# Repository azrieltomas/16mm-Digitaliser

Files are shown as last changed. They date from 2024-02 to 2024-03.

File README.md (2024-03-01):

# 16mm Digitaliser
A slight improvement on the [8mm Digitaliser](https://github.com/azrieltomas/8mm-Digitaliser)
This is currently a work in progress and not fully implemented.

### Design
The hardware design to capture the frames utilises a constantly running motor, and dual IR sensors to determine when sprocket perforations have passed.
As 5+ frames can fit on the digital capture, photographs are taken every 5 frames. Cropping will be acheived by automatically offsetting the crop zone and exporting to separate images.

### Parts
Parts for aligning the film and holding the sensors are from various 3D prints.

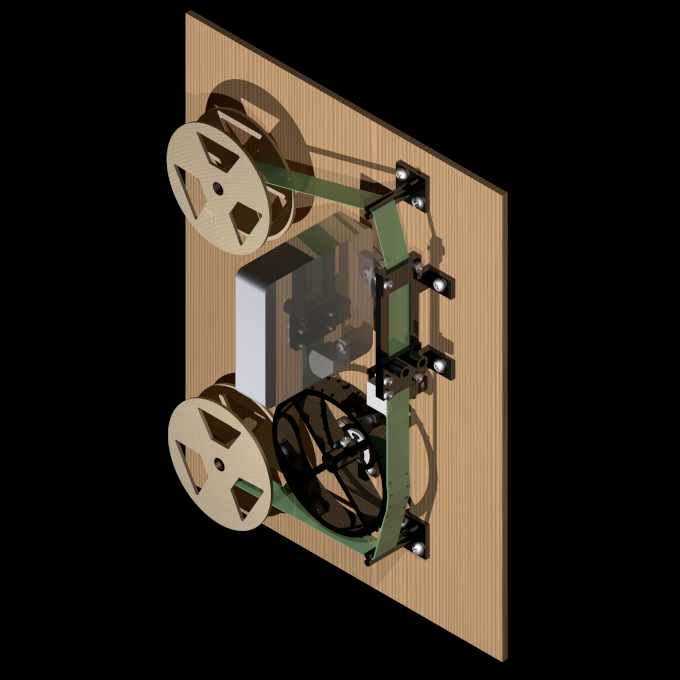
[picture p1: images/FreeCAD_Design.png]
Parts Design
\
*Physical Parts Layout (FreeCAD)*

### Controller
Each perforation sensor has two fine tuning methods:
* Gain (affects sensor output level)
* Cutoff (affects reference level).
The gain and cutoff signals are compared with an LM741 to determine if a perforation is sensed.This is adjustable to compensate for light sections along the film edge that are not perforations, but are still picked up by the sensor.Both perforation sensors are connected by an AND gate to a counter to further filter out non-perforations on single sides of the film.

For single perforation film, a switch sets the sense2 output to always on.

Once the counter has reaches four, it triggers the camera, and resets on five via an AND gate on QA and QC.

The motor can be switched on/off via a buffer circuit. I have used a BUL128 only because I have spares, and they're the only transistor on hand that can handle the motor current. It is probably wise to put a flyback diode on the motor.

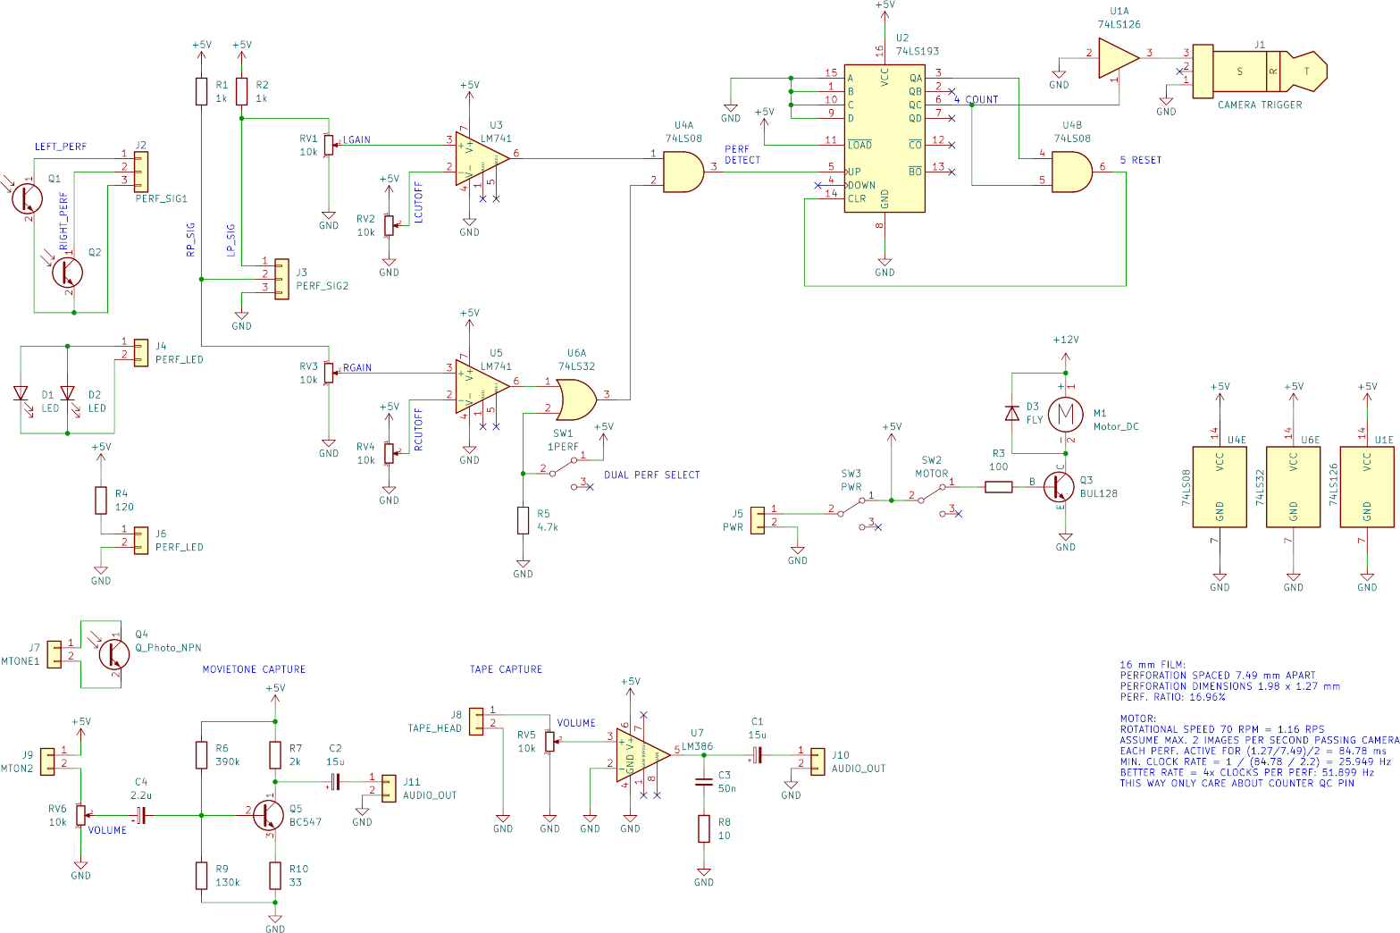
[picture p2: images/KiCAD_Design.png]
Circuit Design
\
*Controller Design (KiCAD)*

### Audio
Audio is captured in two ways, depending on the storage method.
Digital processing can be done by any additional system.

#### Standard magnetic audio
Audio is picked up by a modified cassette tape head and amplified by an LM386 for simplicity.

#### Movietone
Audio is converted by an IR phototransistor - theoretically the same one used for the second set of perforations in dual perf film.
A BC547 amplifier boosts this to line levels.

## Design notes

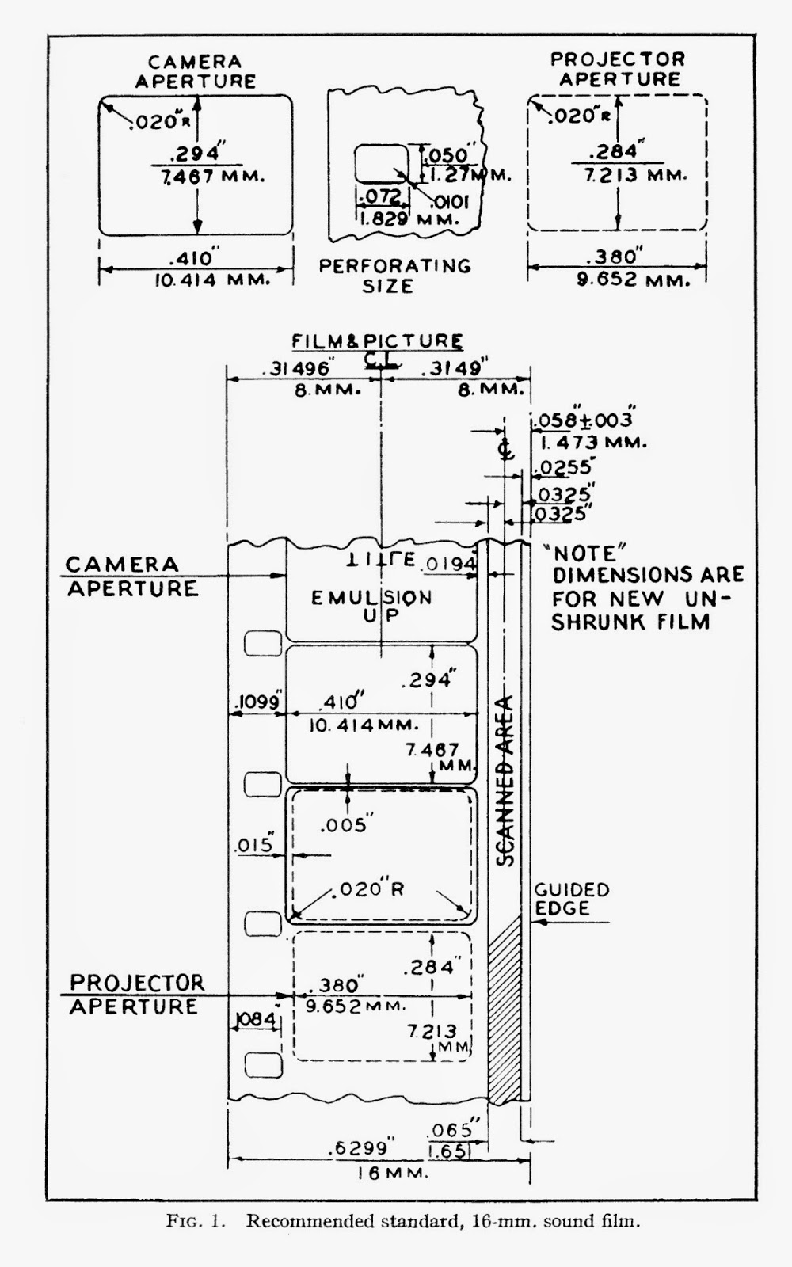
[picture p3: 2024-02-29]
Additional Tools/16mm Sound 1.jpg

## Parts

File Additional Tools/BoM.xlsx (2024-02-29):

Reference | Value | Datasheet | Footprint | Qty | DNP
C1,C2 | 15u | ~ | Capacitor_THT:C_Radial_D6.3mm_H5.0mm_P2.50mm | 2
C3 | 50n | ~ | Capacitor_THT:C_Rect_L4.6mm_W2.0mm_P2.50mm_MKS02_FKP02 | 1
C4 | 2.2u | ~ | Capacitor_THT:C_Radial_D6.3mm_H5.0mm_P2.50mm | 1
D1,D2 | LED | ~ | LED_THT:LED_D5.0mm | 2
D3 | FLY | ~ |  | 1
J1 | CAMERA TRIGGER | ~ | 2.5mm TRS Jack | 1
J2,J3 | Connector_JST:JST_EH_B3B-EH-A_1x03_P2.50mm_Vertical | ~ |  | 1
 |  |  |  | 1
J4,J6 | Connector_JST:JST_EH_B2B-EH-A_1x02_P2.50mm_Vertical | ~ |  | 2
J5,SW3 | PWR | ~ | -- mixed values -- | 2
J7 | MTONE1 | ~ | Connector_JST:JST_EH_B2B-EH-A_1x02_P2.50mm_Vertical | 1
J8 | TAPE_HEAD | ~ | Connector_JST:JST_EH_B2B-EH-A_1x02_P2.50mm_Vertical | 1
J9 | MTON2 | ~ | Connector_JST:JST_EH_B2B-EH-A_1x02_P2.50mm_Vertical | 1
J10,J11 | AUDIO_OUT | ~ | Connector_JST:JST_EH_B2B-EH-A_1x02_P2.50mm_Vertical | 2
J14 | POS1 | ~ | Connector_PinHeader_2.54mm:PinHeader_1x25_P2.54mm_Vertical | 1
J15 | POS2 | ~ | Connector_PinHeader_2.54mm:PinHeader_1x25_P2.54mm_Vertical | 1
J16 | NEG1 | ~ | Connector_PinHeader_2.54mm:PinHeader_1x25_P2.54mm_Vertical | 1
J17 | NEG2 | ~ | Connector_PinHeader_2.54mm:PinHeader_1x25_P2.54mm_Vertical | 1
M1 | Motor_DC | ~ | Connector_JST:JST_EH_B2B-EH-A_1x02_P2.50mm_Vertical | 1
Q1,Q2,Q4 | Q_Photo_NPN | ~ | LED_THT:LED_D5.0mm | 3
Q3 | BUL128 | ~ | Package_TO_SOT_THT:TO-220-3_Vertical | 1
Q5 | BC547 | https://www.onsemi.com/pub/Collateral/BC550-D.pdf | Package_TO_SOT_THT:TO-92_Inline | 1
R1,R2 | 1k | ~ | Resistor_THT:R_Axial_DIN0207_L6.3mm_D2.5mm_P7.62mm_Horizontal | 2
R3 | 100 | ~ | Resistor_THT:R_Axial_DIN0207_L6.3mm_D2.5mm_P7.62mm_Horizontal | 1
R4 | 120 | ~ | Resistor_THT:R_Axial_DIN0207_L6.3mm_D2.5mm_P7.62mm_Horizontal | 1
R5 | 4.7k | ~ | Resistor_THT:R_Axial_DIN0207_L6.3mm_D2.5mm_P7.62mm_Horizontal | 1
R6 | 390k | ~ | Resistor_THT:R_Axial_DIN0207_L6.3mm_D2.5mm_P7.62mm_Horizontal | 1
R7 | 2k | ~ | Resistor_THT:R_Axial_DIN0207_L6.3mm_D2.5mm_P7.62mm_Horizontal | 1
R8 | 10 | ~ | Resistor_THT:R_Axial_DIN0207_L6.3mm_D2.5mm_P7.62mm_Horizontal | 1
R9 | 130k | ~ | Resistor_THT:R_Axial_DIN0207_L6.3mm_D2.5mm_P7.62mm_Horizontal | 1
R10 | 33 | ~ | Resistor_THT:R_Axial_DIN0207_L6.3mm_D2.5mm_P7.62mm_Horizontal | 1
RV1,RV2,RV3,RV4,RV5,RV6 | 10k | ~ | -- mixed values -- | 6
SW1 | 1PERF | ~ | Connector_PinSocket_2.54mm:PinSocket_1x03_P2.54mm_Vertical | 1
SW2 | MOTOR | ~ | Connector_PinSocket_2.54mm:PinSocket_1x03_P2.54mm_Vertical | 1
U1 | 74LS126 | http://www.ti.com/lit/gpn/sn74LS126 | Package_DIP:DIP-14_W7.62mm_Socket | 1
U2 | 74LS193 | http://www.ti.com/lit/ds/symlink/sn74ls193.pdf | Package_DIP:DIP-16_W7.62mm_Socket | 1
U3,U5 | LM741 | http://www.ti.com/lit/ds/symlink/lm741.pdf | Package_DIP:DIP-8_W7.62mm_Socket | 2
U4 | 74LS08 | http://www.ti.com/lit/gpn/sn74LS08 | Package_DIP:DIP-14_W7.62mm_Socket | 1
U6 | 74LS32 | http://www.ti.com/lit/gpn/sn74LS32 | Package_DIP:DIP-14_W7.62mm_Socket | 1
U7 | LM386 | http://www.ti.com/lit/ds/symlink/lm386.pdf | Package_DIP:DIP-8_W7.62mm_Socket | 1

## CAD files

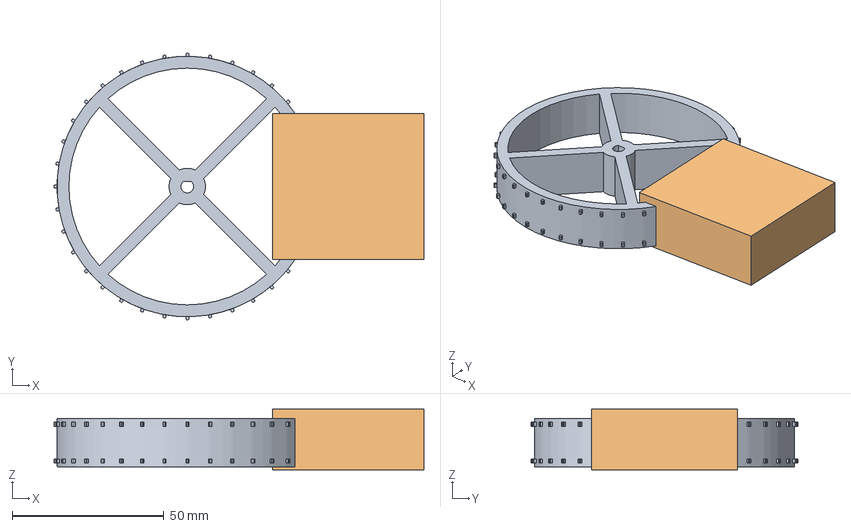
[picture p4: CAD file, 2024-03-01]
3D_Prints/16mm Sprocket.FCStd
121.9 x 87.8 x 20.0 mm

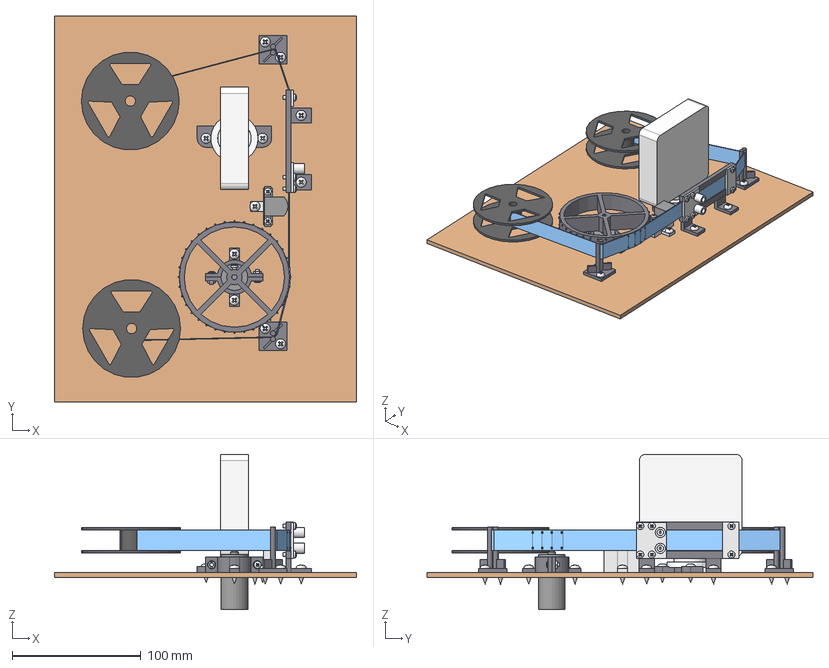
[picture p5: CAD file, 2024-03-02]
3D_Prints/Layout/Layout.FCStd
235.0 x 300.0 x 121.0 mm
Motor
Bracket1
Bracket2
DrivingWheel
MainHolder002
Reel
Horseshoe
Lamp
TapeHead
Reel001
Guide
Guide001
Base
Film
TapeHeadBase
4 mmx12-Screw
4 mmx12-Screw001
4 mmx12-Screw002
4 mmx12-Screw003
4 mmx12-Screw004
4 mmx12-Screw005
4 mmx12-Screw006
4 mmx12-Screw007
4 mmx12-Screw008
4 mmx12-Screw009
4 mmx12-Screw010
M3x8-Screw
M3-Nut
M3-Nut001
M3x8-Screw001
4 mmx12-Screw011
4 mmx12-Screw012
M3x8-Screw013
M3x8-Screw003
M3x8-Screw005
M3x8-Screw007
M3x8-Screw008
M3x8-Screw009
M3x8-Screw010
M3x8-Screw011
M3x8-Screw012
TopCover001
BottomCover001

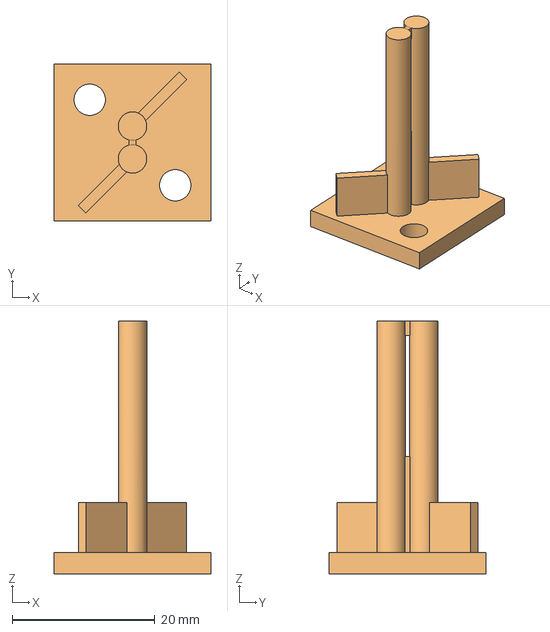
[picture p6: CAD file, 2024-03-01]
3D_Prints/16mm Film Guide.FCStd
22.0 x 22.0 x 35.5 mm

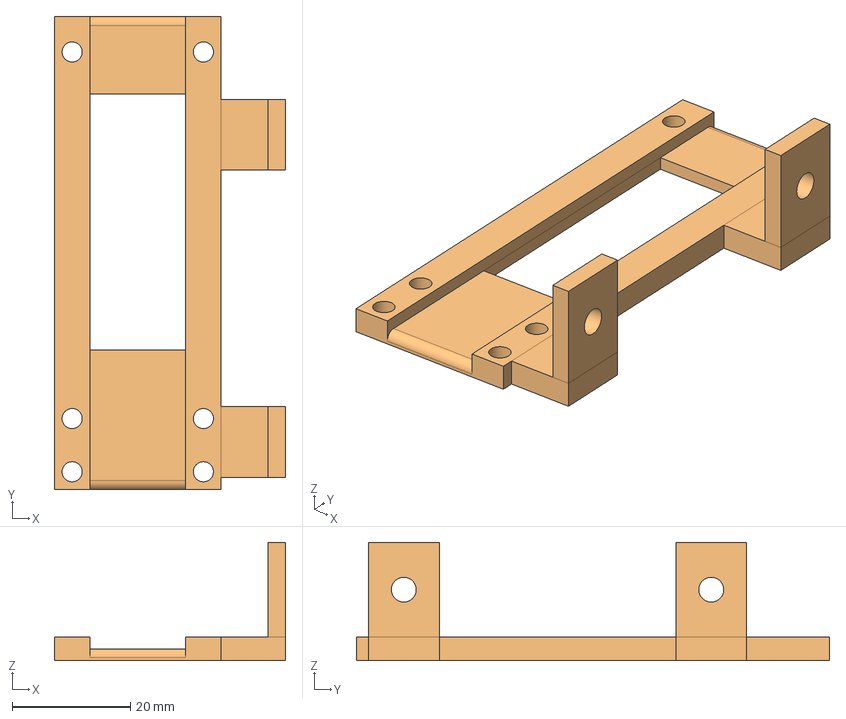
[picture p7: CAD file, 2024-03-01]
3D_Prints/16mm Film Holder.FCStd
39.1 x 80.0 x 20.0 mm
MainHolder
MainHolder001

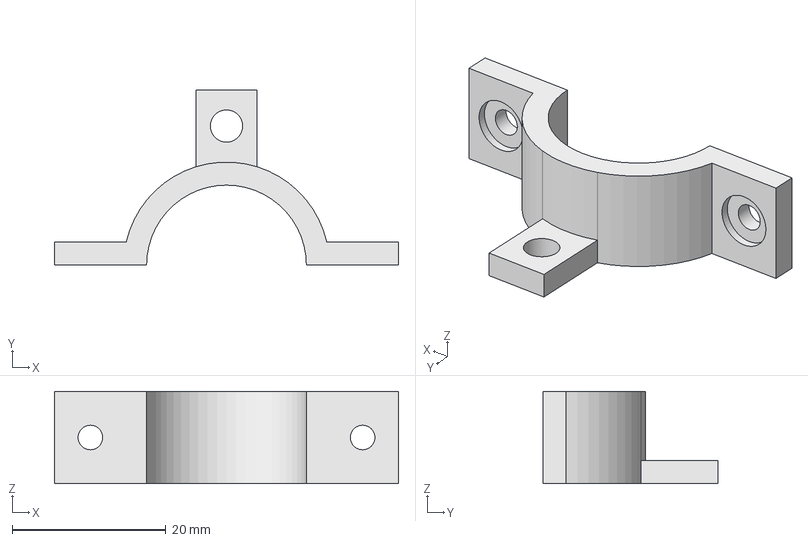
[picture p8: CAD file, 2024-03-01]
3D_Prints/Motor Bracket.FCStd
44.8 x 22.8 x 12.0 mm

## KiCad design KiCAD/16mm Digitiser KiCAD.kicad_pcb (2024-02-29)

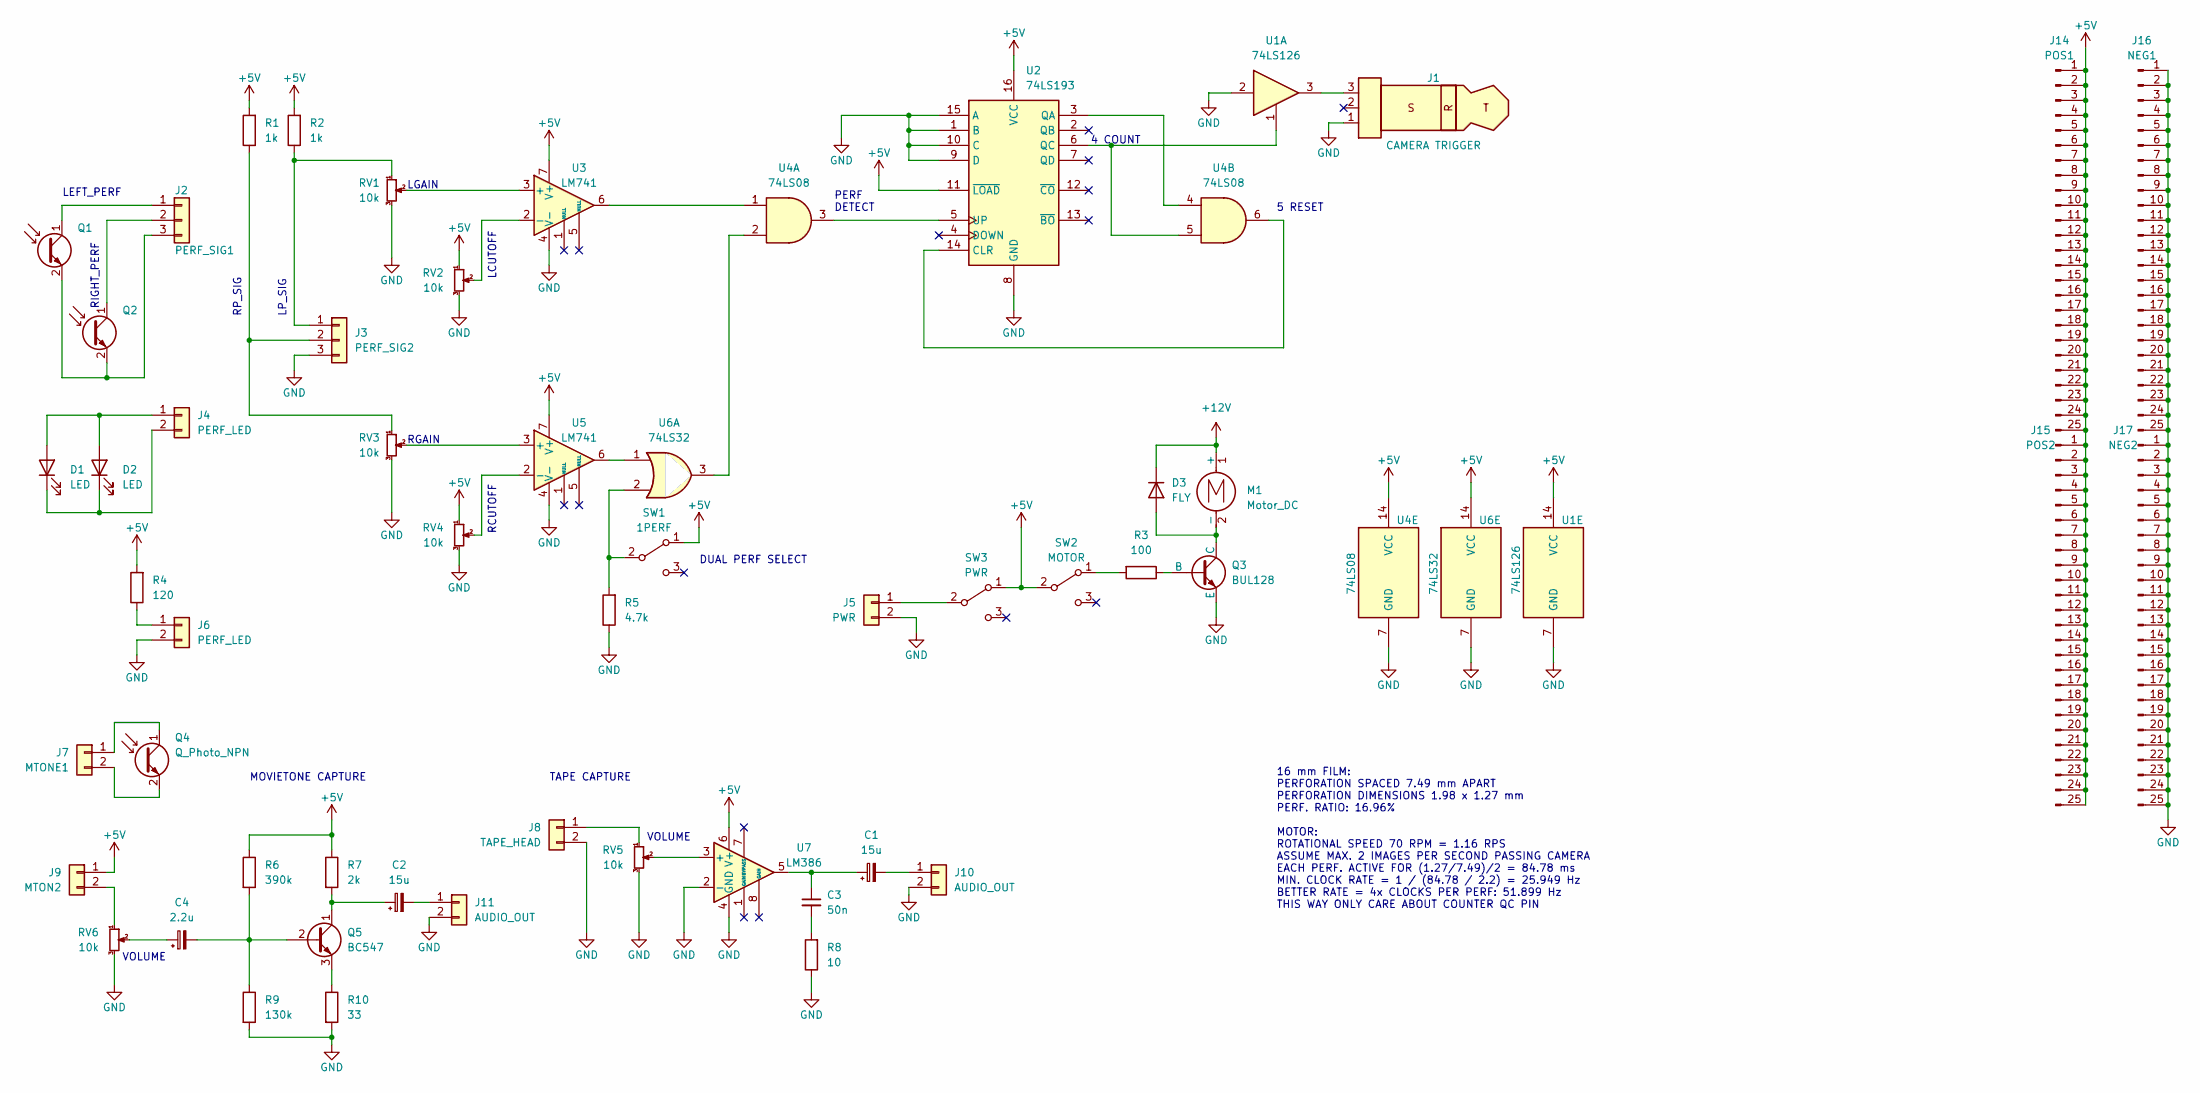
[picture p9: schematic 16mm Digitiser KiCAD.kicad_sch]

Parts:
C1, C2: 15u; C_Radial_D6.3mm_H5.0mm_P2.50mm
C3: 50n; C_Rect_L4.6mm_W2.0mm_P2.50mm_MKS02_FKP02
C4: 2.2u; C_Radial_D6.3mm_H5.0mm_P2.50mm
D1, D2: LED; LED_D5.0mm
D3: FLY
J1: CAMERA TRIGGER; JST_EH_B3B-EH-A_1x03_P2.50mm_Vertical
J2: PERF_SIG1; JST_EH_B3B-EH-A_1x03_P2.50mm_Vertical
J3: PERF_SIG2; JST_EH_B3B-EH-A_1x03_P2.50mm_Vertical
J4, J6: PERF_LED; JST_EH_B2B-EH-A_1x02_P2.50mm_Vertical
J5: PWR; JST_EH_B2B-EH-A_1x02_P2.50mm_Vertical
J7: MTONE1; JST_EH_B2B-EH-A_1x02_P2.50mm_Vertical
J8: TAPE_HEAD; JST_EH_B2B-EH-A_1x02_P2.50mm_Vertical
J9: MTON2; JST_EH_B2B-EH-A_1x02_P2.50mm_Vertical
J10, J11: AUDIO_OUT; JST_EH_B2B-EH-A_1x02_P2.50mm_Vertical
J14: POS1; PinHeader_1x25_P2.54mm_Vertical
J15: POS2; PinHeader_1x25_P2.54mm_Vertical
J16: NEG1; PinHeader_1x25_P2.54mm_Vertical
J17: NEG2; PinHeader_1x25_P2.54mm_Vertical
M1: Motor_DC; JST_EH_B2B-EH-A_1x02_P2.50mm_Vertical
Q1, Q2, Q4: Q_Photo_NPN; LED_D5.0mm
Q3: BUL128; TO-220-3_Vertical
Q5: BC547; TO-92_Inline
R1, R2: 1k; R_Axial_DIN0207_L6.3mm_D2.5mm_P7.62mm_Horizontal
R3: 100; R_Axial_DIN0207_L6.3mm_D2.5mm_P7.62mm_Horizontal
R4: 120; R_Axial_DIN0207_L6.3mm_D2.5mm_P7.62mm_Horizontal
R5: 4.7k; R_Axial_DIN0207_L6.3mm_D2.5mm_P7.62mm_Horizontal
R6: 390k; R_Axial_DIN0207_L6.3mm_D2.5mm_P7.62mm_Horizontal
R7: 2k; R_Axial_DIN0207_L6.3mm_D2.5mm_P7.62mm_Horizontal
R8: 10; R_Axial_DIN0207_L6.3mm_D2.5mm_P7.62mm_Horizontal
R9: 130k; R_Axial_DIN0207_L6.3mm_D2.5mm_P7.62mm_Horizontal
R10: 33; R_Axial_DIN0207_L6.3mm_D2.5mm_P7.62mm_Horizontal
RV1, RV2, RV3, RV4: 10k; Potentiometer_ACP_CA9-V10_Vertical
RV5, RV6: 10k; Potentiometer_Alps_RK163_Single_Horizontal
SW1: 1PERF; PinSocket_1x03_P2.54mm_Vertical
SW2: MOTOR; PinSocket_1x03_P2.54mm_Vertical
SW3: PWR; PinSocket_1x03_P2.54mm_Vertical
U1: 74LS126; DIP-14_W7.62mm_Socket
U2: 74LS193; DIP-16_W7.62mm_Socket
U3, U5: LM741; DIP-8_W7.62mm_Socket
U4: 74LS08; DIP-14_W7.62mm_Socket
U6: 74LS32; DIP-14_W7.62mm_Socket
U7: LM386; DIP-8_W7.62mm_Socket

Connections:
+5V: J9.1, J14.1, J14.2, J14.3, J14.4, J14.5, J14.6, J14.7, J14.8, J14.9, J14.10, J14.11, J14.12, J14.13, J14.14, J14.15, J14.16, J14.17, J14.18, J14.19, J14.20, J14.21, J14.22, J14.23, J14.24, J14.25, J15.1, J15.2, J15.3, J15.4, J15.5, J15.6, J15.7, J15.8, J15.9, J15.10, J15.11, J15.12, J15.13, J15.14, J15.15, J15.16, J15.17, J15.18, J15.19, J15.20, J15.21, J15.22, J15.23, J15.24, J15.25, R1.2, R2.2, R4.2, R6.1, R7.1, RV2.1, RV4.1, SW1.1 (A), SW2.2 (B), SW3.1 (A), U1.14 (VCC), U2.11 (~LOAD), U2.16 (VCC), U3.7 (V+), U4.14 (VCC), U5.7 (V+), U6.14 (VCC), U7.6 (V+)
+12V: D3.1 (K), M1.1 (+)
GND: J1.1, J3.3, J5.2, J6.2, J8.2, J10.2, J11.2, J16.1, J16.2, J16.3, J16.4, J16.5, J16.6, J16.7, J16.8, J16.9, J16.10, J16.11, J16.12, J16.13, J16.14, J16.15, J16.16, J16.17, J16.18, J16.19, J16.20, J16.21, J16.22, J16.23, J16.24, J16.25, J17.1, J17.2, J17.3, J17.4, J17.5, J17.6, J17.7, J17.8, J17.9, J17.10, J17.11, J17.12, J17.13, J17.14, J17.15, J17.16, J17.17, J17.18, J17.19, J17.20, J17.21, J17.22, J17.23, J17.24, J17.25, Q3.3 (E), R5.1, R8.1, R9.2, R10.2, RV1.3, RV2.3, RV3.3, RV4.3, RV5.3, RV6.3, U1.2, U1.7 (GND), U2.1 (B), U2.8 (GND), U2.9 (D), U2.10 (C), U2.15 (A), U3.4 (V-), U4.7 (GND), U5.4 (V-), U6.7 (GND), U7.2 (-), U7.4 (GND)
unnamed: C1.1, C3.1, U7.5
unnamed: C3.2, R8.2
unnamed: C4.1, RV6.2
unnamed: D1.2 (A), D2.2 (A), J4.1
unnamed: D1.1 (K), D2.1 (K), J4.2
unnamed: J1.3, U1.3
unnamed: J2.1, Q1.1 (C)
unnamed: J2.2, Q2.1 (C)
unnamed: J2.3, Q1.2 (E), Q2.2 (E)
unnamed: J3.1, R2.1, RV1.1
unnamed: J3.2, R1.1, RV3.1
unnamed: J5.1, SW3.2 (B)
unnamed: J6.1, R4.1
unnamed: J7.1, Q4.1 (C)
unnamed: J7.2, Q4.2 (E)
unnamed: J8.1, RV5.1
unnamed: J9.2, RV6.1
unnamed: C1.2, J10.1
unnamed: C2.2, J11.1
unnamed: D3.2 (A), M1.2 (-), Q3.1 (C)
unnamed: Q3.2 (B), R3.1
unnamed: C4.2, Q5.2 (B), R6.2, R9.1
unnamed: C2.1, Q5.1 (C), R7.2
unnamed: Q5.3 (E), R10.1
unnamed: R5.2, SW1.2 (B), U6.2
unnamed: R3.2, SW2.1 (A)
unnamed: U2.14 (CLR), U4.6
unnamed: U2.3 (QA), U4.4
unnamed: U2.5 (UP), U4.3
unnamed: RV1.2, U3.3 (+)
unnamed: RV2.2, U3.2 (-)
unnamed: U3.6, U4.1
unnamed: U4.2, U6.3
unnamed: RV3.2, U5.3 (+)
unnamed: RV4.2, U5.2 (-)
unnamed: U5.6, U6.1
unnamed: RV5.2, U7.3 (+)

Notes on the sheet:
LP_SIG
LGAIN
RIGHT_PERF
4 COUNT
LEFT_PERF
RP_SIG
LCUTOFF
VOLUME
RGAIN
RCUTOFF
DUAL PERF SELECT
MOVIETONE CAPTURE
16 mm FILM: PERFORATION SPACED 7.49 mm APART PERFORATION DIMENSIONS 1.98 x 1.27 mm PERF. RATIO: 16.96% MOTOR: ROTATIONAL SPEED 70 RPM = 1.16 RPS ASSUME MAX. 2 IMAGES PER SECOND PASSING CAMERA EACH PERF. ACTIVE FOR (1.27/7.49)/2 = 84.78 ms MIN. CLOCK RATE = 1 / (84.78 / 2.2) = 25.949 Hz BETTER RATE 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
TAPE CAPTURE
PERF DETECT
5 RESET

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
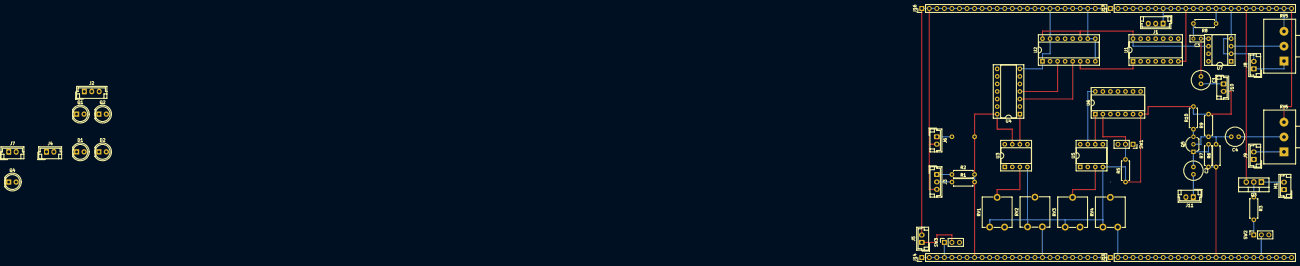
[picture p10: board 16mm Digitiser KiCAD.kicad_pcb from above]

Board: 4 copper layers, 53 parts (1 on the bottom side), 41 nets.

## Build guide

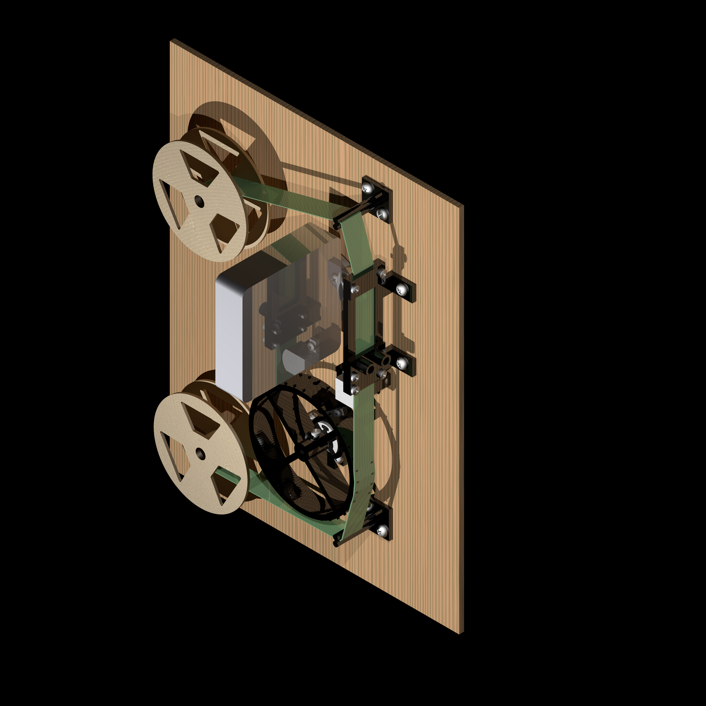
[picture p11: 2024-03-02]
3D_Prints/Layout/Layout.png

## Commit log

2024-02-29 first issue
    [16mm Digitiser KiCAD.kicad_pcb, 16mm Digitiser KiCAD.kicad_sch, 16mm Film Guide.FCStd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]
2024-03-01 cad designs
    [16mm Film Guide.FCStd, 16mm Film Holder.FCStd, 16mm Sprocket.FCStd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]
2024-03-01 design layout
    [16mm Film Guide.FCStd, 16mm Film Holder.FCStd, 16mm Sprocket.FCStd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]
2024-03-01 move layout to own folder
    [Layout.FCStd]
2024-03-02 3D rendering
    [Layout.FCStd]
